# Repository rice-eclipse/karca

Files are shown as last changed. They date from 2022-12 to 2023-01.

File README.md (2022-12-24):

# kARCA: An engine controller PCB for Rice Eclipse

kARCA is Rice Eclipse's next generation of engine controller boards.
Its intended use is for data collection and valve actuation control on the Titan and Proxima rocket
motors.

It was designed in 2022 by Rice Eclipse.

## Usage

This board was designed in [KiCAD](https://www.kicad.org/).
Exports (such as gerber files) should be stored in the `target` directory (covered by gitignore).

It connects to a Raspberry Pi running our custom controller software,
[`slonk`](https://github.com/rice-eclipse/slonk), which in turn interfaces with the user dashboard
[`slonkboard`](https://github.com/rice-eclipse/slonkboard).

## Further documentation

A full overview of the design of kARCA is available in [docs/karca.md](docs/karca.md).

## License

This design is licensed under the Creative Commons Attribution-ShareAlike 4.0 International license
(CC BY-SA 4.0).

For more information, refer to [LICENSE.md](LICENSE.md).

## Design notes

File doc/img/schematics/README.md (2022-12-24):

# How to generate these files

In order to generate the SVG files in this directory, simply navigate to the top level of the
`kARCA` schematic and run `File -> Plot` with this directory as the target directory.

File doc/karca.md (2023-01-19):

# kARCA Design Outline

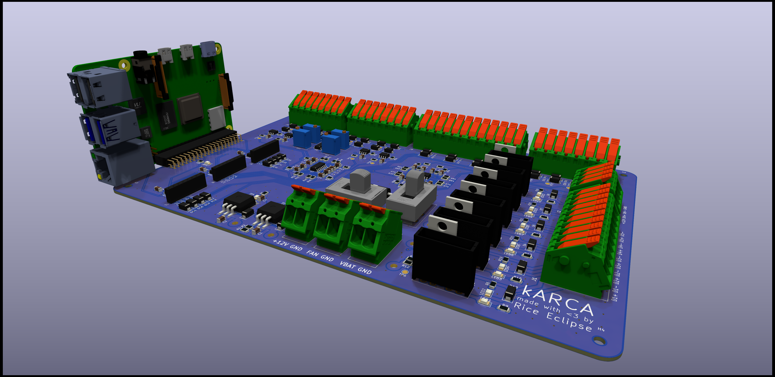
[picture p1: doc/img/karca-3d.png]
3D render of kARCA PCB.


This design outline is inteded as a reference for future Rice Eclipse members who either need to
edit the design of kARCA or better understand it.

It is also intended to be a comprehensive spec for working with the board.

## Project Motivation

Rice Eclipse is a student-run organization which designs, builds, and tests its own rocket motors.
To furnish this process, we build our own engine controller electronics systems from scratch.
`kARCA` is the latest revision of Eclipse's controller hardware: it communicates with a user-facing
dashboard to allow the user to control the engine in real time.

`kARCA` is part of a larger hardware and software stack which is essential to Eclipse's engine
testing system.
The user-facing dashboard, [`slonkboard`](https://github.com/rice-eclipse/slonkboard) is a
front-end application which allows mission control to easily use the controller.
Inside of the `kARCA` controller, a Raspberry Pi runs the controller software, `slonk`, which
receives messages from `slonkboard` and executes them, while also logging data and transmitting it
to `slonkboard`.

`kARCA` is intended as a replacement to an older control board, called the "Mk1.1 engine
controller."
The main reason for this replacement is because it's showing its age: the Mk1.1 controller was
designed for smaller valves and with fewer capabilities than its replacement.
In addition, a fire caused irreparable damage to one of the pressure transducer amplifiers on the
controller hardware.

## Requirements

kARCA has a few client needs that it must support for Rice Eclipse's Titan and Proxima rocket
motors.
It must:

1. Collect data from 4 load cells.
1. Collect data from 4 pressure transducers.
1. Collect data from 4 thermocouples.
1. Control the ignition system, driving up to 50 amps at 12 volts to the igniters.
1. Control 5 valves, each consuming up to 1 amp at 12 volts, by user command.
1. Transmit real-time data on load cells, pressure transducers, thermocouples, and valve actuation
   states to the user.

## Design

### Power regulation

Linear dropout regulators.

Power management consists of 3 separate voltage levels: 12 volts, 10 volts, and 5 volts.

The 12 volt lines are used for powering the solenoid driver circuits, the router, and the fan.
The 10 volt line is used for powering the analog amplification hardware (with the exception of the
load cell instrumentation amplifiers) and the pressure transducers.
The 5 volt line is used for powering the Raspberry Pi, the ADCs, the instrumentation amplifiers,
the thermocouple breakout boards, and the load cell.

The 5 volt and 10 volt lines are both supplied by linear dropout (LDO) regulators.
These regulators have the benefit of being stupid-simple at the cost of poor efficiency.
We've included flyback Schottky diodes on each regulator to hopefully reduce the risk of
reverse-biasing damanging the regulators.

_Note for future designs: it is possible to remove the 10V line from the design and substitute the
12V line.
The 10V line was only kept for backward compatibility, not for any material value._

The status light LED13 is lit when power is supplied to the 12V battery line.
LED14 and LED15 are lit when the LDO regulators for 10V and 5V respectively are working.

### Data collection

#### Load cells

Load cell amplification and filtering.

A load cell is a linear device used to measure force.
Power is supplied to the load cell through a positive and negative terminal, and then the load cell
returns a differential output.
The differential voltage $V_{\mathit{dm}}$ grows linearly with the force on the load cell.
If the voltage given to the load cell is $V_{\mathit{DD}}$, the output voltage $V_{\mathit{dm}}$ is
linearly proportional to the input voltage and the load $F$ via the constants $r$ and $FS$.

$$
V_{\mathit{dm}} = \frac{r}{\mathit{FS}} V_{\mathit{DD}} F
$$

$\mathit{FS}$ is the full-scale force of the load cell, and $r$ is the mV/V rating of the load cell.
Typically, $r$ is very small, so a high amount of amplification is needed to get an ADC-readable
signal.
Additionally, since $V_{\mathit{dm}}$ is a differential-mode signal, we must use an instrumentation
amplifier to convert the differential voltage to an absolute voltage.

On `kARCA`, there are two amplification stages for each load cell channel.
The first stage is an instrumentation amplifier, which amplifies the voltage measured and also
shifts the signal to a differential-mode value.
The second stage is an anti-aliasing filter, which low-passes the analog signal from the
instrumentation amplifier and also amplifies it further.

The total gain in the load cell amplifier is the product of the gains of the two stages.
The instrumentation amplifier has a gain of
$1 + \frac{20 \text{k} \Omega}{200 \Omega} = 101$, while the anti-aliasing filter has a
gain of $1 + \frac{15 \text{k} \Omega}{10 \text{k} \Omega} = 2.5$, yielding a final gain of 252.5.

The
[load cell for the Titan rocket motor](https://prod-edam.honeywell.com/content/dam/honeywell-edam/sps/siot/en-us/products/test-and-measurement-products/load-cells/low-profile/model-41-series/documents/sps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)
has a scale of 3mV/V and a full-scale force of 3000, yielding an output voltage equal to the load
$F$ times $1.2625 \frac{\text{mV}}{\text{lb f}}$.
This corresponds to a full-scale range of 3960 lb f.

At extremely high loads, the load cell amplifier could ouput voltages greater than 5 V to the ADC.
This would likely damage the ADC, so we included Schottky diodes to clamp the voltage below 5.5 V.

#### Pressure transducers

Pressure transducer anti-aliasing and amplifier.

Our pressure transducers are 4-20 mA devices.
This means that when supplied with a voltage greater than 8 V, the pressure transducers will pull
a current as an affine transform of the pressure (4 mA for 0 psi g, and 20 mA for 1000 psi g).

To convert the current to a voltage, we place the pressure transducer in series with a 22 $\Omega$
resistor, yielding an input voltage between 0.088 and 0.44 V.
Since the supply voltage is 10 V, the voltage given to the pressure transducer will never be below
9.66 V, which leaves plenty of headroom past the minimum 8 V requirement.

We then amplify the input voltage by a gain of 10.22, yielding a minimum output voltage of 0.898 V
and a maximum of 4.5 V.
Although we aren't using the full scale, it's "good enough" for our needs, giving us a resolution of
0.34 psi.
The gain of the amplifier is determined by the ratio of the feeback and gain resistors on the output
of the amplifier.
The gain for each channel is the same, so we only provide a sample formula for PT1's gain below.

$$
G = 1 + \frac{R_{73}}{R_{75}}
$$

Additionally, we anti-alias the pressure transducer signal with a two-pole Sallen-Key low-pass
filter.
The cutoff frequency is identical across all four PT channels, and is determined by the values of the input resistors and capacitors in the amplifier.
We provide a sample formula for PT1's gain below.

$$
f_c = \frac{1}{2 \pi \sqrt{R_{68} R_{69} C_{28} C_{26}}}
$$

Since the pressure transducer anti-aliasing amplifier is supplied by 10 V, we also include a set of
Schottky diodes to prevent the amplifier from sending too high of a voltage to the ADC.

#### Thermocouples

Thermocouple schematics.

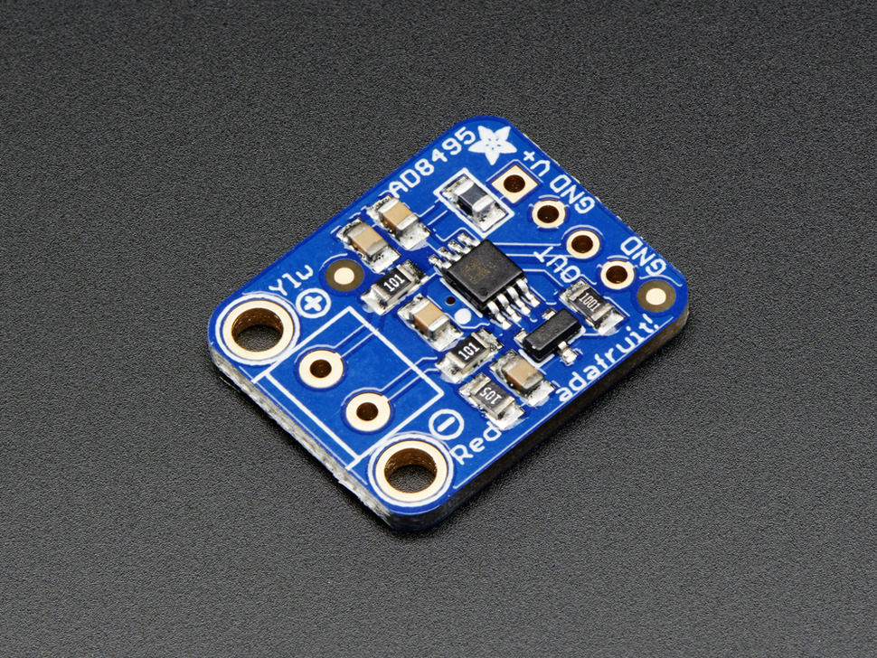
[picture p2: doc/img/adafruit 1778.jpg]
Adafruit AD8495 amplifier.


We use an [Adafruit AD8495](https://www.adafruit.com/product/1778) (part number 1778) amplifier
breakout board, which gives a voltage between 0 and 5V as an affine function of the measured
thermocouple temperature.
As a result, no amplification is needed and we can simply run the result directly to the ADC.
This makes the thermocouple data acquisition the easiest part of the design.
On the board end, only 3 connections are needed: positive voltage source, ground, and an analog
input.

However, the breakout board used only supports K-type thermocouples.
If, in the future, we decide to use other thermocouples, we may need to consider other avenues of
approach.

### Valve actuation

Valve drivers and ignition driver.

### Ignition system

As far as the `kARCA` PCB is concerned, the ignition system is just another valve.
Externally, though, the ignition system is a two-step sequence of relays.

## Pinouts

This is intended as a reference for programmers working on `slonk`,

### Raspberry Pi

| Number | Raspberry Pi function | GPIO ID | Board function |
| -----: | --- | ---: | --- |
| 1 | +3.3V | - | - |
| 2 | +5V | - | +5V |
| 3 | GPIO | 2 | - |
| 4 | +5V | - | +5V |
| 5 | GPIO | 3 | - |
| 6 | GND | - | GND |
| 7 | GPIO | 4 | - |
| 8 | UART0 TX | 14 | - |
| 9 | GND | - | GND |
| 10 | UART0 RX | 15 | - |
| 11 | GPIO | 17 | Driver 6 control |
| 12 | GPIO | 18 | - |
| 13 | GPIO | 27 | Driver 5 control |
| 14 | GND | - | GND |
| 15 | GPIO | 23 | Driver 4 control |
| 16 | GPIO | 23 | - |
| 17 | +3.3V | - | - |
| 18 | GPIO | 24 | - |
| 19 | SPI0 MOSI | 10 | SPI MOSI |
| 20 | GND | - | GND |
| 21 | SPI0 MISO | 9 | SPI MISO |
| 22 | GPIO | 25 | ADC1 CS |
| 23 | SPI0 SCLK | 11 | SPI CLK |
| 24 | SPI0 CS0 | 8 | ADC2 CS |
| 25 | GND | - | GND |
| 26 | SPI0 CS1 | 7 | ADC3 CS |
| 27 | I2C EEPROM data | - | - |
| 28 | I2D EEPROM clock | - | - |
| 29 | GPIO | 5 | Heartbeat |
| 30 | GND | - | GND |
| 31 | GPIO | 6 | Driver 3 control |
| 32 | GPIO | 12 | - |
| 33 | GPIO | 13 | Driver 2 control |
| 34 | GND | - | GND |
| 35 | GPIO | 19 | Driver 1 control |
| 36 | GPIO | 16 | - |
| 37 | GPIO | 26 | - |
| 38 | GPIO | 20 | - |
| 39 | GND | - | GND |
| 40 | GPIO | 21 | - |

### ADC1 - Load cells

| Channel | Use |
| --- | --- |
| 0 | LC1 |
| 1 | LC2 |
| 2 | LC3 |
| 3 | LC4 |
| 4 | unused |
| 5 | unused |
| 6 | unused |
| 7 | unused |

### ADC2 - Pressure transducers

| Channel | Use |
| --- | --- |
| 0 | PT1 |
| 1 | PT2 |
| 2 | PT3 |
| 3 | PT4 |
| 4 | unused |
| 5 | unused |
| 6 | unused |
| 7 | unused |

### ADC3 - Thermocouples

| Channel | Use |
| --- | --- |
| 0 | TC1 |
| 1 | TC2 |
| 2 | TC3 |
| 3 | TC4 |
| 4 | unused |
| 5 | unused |
| 6 | unused |
| 7 | unused |

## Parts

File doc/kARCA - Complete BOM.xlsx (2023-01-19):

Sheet: Totals
GRAND TOTAL: | $447.39

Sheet: Box
Ordered | Vendor | Manufacturer | Part Number | Description | Price | Quantity/package | Quantity/Assembly | Quantity to Purchase | Total price | Comments | Link
x | Amazon | GDQLCNXB |  | 5-pin XLR female connector | $12.99 | 5 | 4 | 1 | $12.99 |  | https://www.amazon.com/GDQLCNXB-Speaker-Microphone-Connector-Housing/dp/B0B1X4JXYX
x | Amazon | CNLINKO |  | 2-pin LP20 connector set | $15.99 | 1 | 3 | 4 | $63.96 |  | https://www.amazon.com/CNLINKO-waterproof-connector-locking-connect/dp/B07WJRWCJ2
x | Amazon | Zulkit | NBF-32422 | Plastic Electrical Box | $115.99 | 1 | 1 | 1 | $115.99 | consider alternatives if it goes out of stock | https://www.amazon.com/dp/B09YTYJP1N/ref=twister_B07RPNWC8V?_encoding=UTF8&th=1
x | Amazon | Gebildet |  | JD1912 Car Relay Harness 12V 40A | $8.49 | 2 | 1 | 1 | $8.49 |  | https://www.amazon.com/ARTGEAR-Harness-Color-Labeled-Automotive-Motorcycle/dp/B078T8CMF6?th=1
 | Amazon | Ximoon |  | 12V Power Trim Solenoid Switch | $13.99 | 1 | 1 | 1 | $13.99 |  | https://www.amazon.com/Ximoon-Solenoid-Outboard-89-96158T-89-846070/dp/B07JRC7WJ2
 | Amazon | Piezo |  | Piezo Buzzer 12V 100dB | $9.99 | 2 | 1 | 1 | $9.99 |  | https://www.amazon.com/Icstation-85dB-Active-Piezo-Electronic/dp/B01LAYWUDO
 | Amazon | DaierTek |  | 12 Volt Toggle Switch Safety Cover Guard | $7.99 | 1 | 1 | 1 | $7.99 |  | https://www.amazon.com/DaierTek-125VAC-Waterproof-Automotive-Aircraft/dp/B07T6YNRZS
 | Amazon | Monoprice |  | flat cat5 cable 3ft | $4.31 | 1 | 1 | 1 | $4.31 |  | https://www.amazon.com/Monoprice-Cat5e-Ethernet-Patch-Cable/dp/B00ACR5SD0
 | Amazon |  |  | Anderson connector kit | $15.98 |  |  |  | $15.98 |  | https://www.amazon.com/Powerpole-Connectors-Assortment-Disconnect-Unassembled/dp/B07CB121LL
 | McMaster-Carr |  | 90975A002 | Tee Nut, #4-40 | $14.46 | 100 | 4 | 1 | $14.46 |  | https://www.mcmaster.com/90975A002/
 | McMaster-Carr |  | 96068A105 | Thread Forming Screw for Plastic, No.4 x 0.5" Long | $6.18 | 100 | 36 | 1 | $6.18 | Mounting screws for XLR connectors | https://www.mcmaster.com/90434A115/
 | McMaster-Carr |  | 9697T3 | 14AWG Paired Red/Black Wire - 25 Feet | $18.75 | 1 | 1 | 1 | $18.75 |  | https://www.mcmaster.com/9697T3/
 | McMaster-Carr |  | 8054T13 | 22AWG Red Wire - 25 Feet | $3.58 | 1 | 1 | 1 | $3.58 |  | https://www.mcmaster.com/8054T13
 | McMaster-Carr |  | 8054T13 | 22AWG Black Wire - 25 Feet | $3.58 | 1 | 1 | 1 | $3.58 |  | https://www.mcmaster.com/8054T13
 | McMaster-Carr |  | 8054T13 | 22AWG Blue Wire - 25 Feet | $3.58 | 1 | 1 | 1 | $3.58 |  | https://www.mcmaster.com/8054T13
 | McMaster-Carr |  | 8054T13 | 22AWG White Wire - 25 Feet | $3.58 | 1 | 1 | 1 | $3.58 |  | https://www.mcmaster.com/8054T13
 | McMaster-Carr |  | 8054T13 | 22AWG Green Wire - 25 Feet | $3.58 | 1 | 1 | 1 | $3.58 |  | https://www.mcmaster.com/8054T13
 | Mouser | Amphenol | 523-AC3FAV-AU-PRE | 3-pin XLR female connector | $0.81 | 1 | 13 | 15 | $12.18 |  | https://www.mouser.com/ProductDetail/Amphenol-Audio/AC3FAV1-AU-PRE?qs=4QugYJNEYLfIiuxU%2Fbda%252Bw%3D%3D
 | OEDK |  |  | 1/4" thick plywood bottom board for box | $5.00 | 1 | 1 | 1 | $5.00
 | Wire | Wire
 |  |  |  |  |  |  |  | TOTAL: | $328.16

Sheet: Sensors and External Components
Vendor | Manufacturer | Part Number | Description | Price | Quantity/package | Quantity/Assembly | Quantity to Purchase | Total price | Comments | Link
 | Honeywell | 41-DN | 3000lb Pancake Load Cell; 3mV/V |  | 1 | 1 | 0 |  | Titan II load cell | https://prod-edam.honeywell.com/content/dam/honeywell-edam/sps/siot/en-us/products/test-and-measurement-products/load-cells/low-profile/model-41-series/docume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
 | Phidgets | CZL301C | 100kg (220lb) S-Type Load Cell | $45.00 | 1 | 1 | 0 |  | Luna/Proxima load cell | https://www.phidgets.com/?tier=3&catid=9&pcid=7&prodid=229
 | Omega | PX119-1KGI | Pressure Transducer, 4-20mA, 0-1000psig |  | 1 | 4 | 0 |  | Pressure transducer | https://assets.omega.com/pdf/test-and-measurement-equipment/pressure/pressure-transducers/PX119.pdf
 | Adafruit | 270 | Thermocouple, Type-K, 900C | $9.95 | 1 | 3 | 0 |  | Non-oxidizer thermocouples | https://www.adafruit.com/product/270
 | Adafruit | 1778 | Analog Output K-Type Thermocouple Amplifier - AD8495 Breakout | $11.95 | 1 | 4 | 0 |  |  | https://www.adafruit.com/product/1778

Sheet: PCB (assembled by Eclipse)
Vendor | Vendor Number | Manufacturer | Description | Price | Quantity/package | Quantity/Assembly | Quantity to Purchase | Total price | Comments | Link
JLC |  |  | ARCA PCB |  |  | 1 | 5 |  | JLC requires minimum purchase of 5 PCBs, of which 2 is the minimum amount to buy assembled. Price should include all parts assembled by JLC as well.
Connectors
Mouser | 200-SSQ12002GDRA | Samtec | 2x20 90 degree female header connector | $10.72 | 1 | 1 | 1 | $10.72 | Raspberry Pi connector. Consider buying cheaper from Adafruit? | https://www.mouser.com/ProductDetail/Samtec/SSQ-120-02-G-D-RA?qs=rU5fayqh%252BE1h5x2E2Y6bfA%3D%3D
Mouser | 571-215297-8 | TE Connectivity | 1x8 Header Pin Female | $1.61 | 1 | 3 | 3 | $4.83
Mouser | 651-1190370 | Phoenix Contact | LPTA 8 Position Connector | $5.78 | 1 | 3 | 3 | $17.34
Mouser | 651-1190363 | Phoenix Contact | LPTA 2 Position Connector | $1.44 | 1 | 3 | 3 | $4.32
Mouser | 651-1190365 | Phoenix Contact | LPTA 4 Position Connector | $2.84 | 1 | 1 | 1 | $2.84
Mouser | 651-1190372 | Phoenix Contact | LPTA 10 Position Connector | $7.20 | 1 | 1 | 1 | $7.20
Mouser | 651-1190374 | Phoenix Contact | LPTA 12 Position Connector | $8.65 | 1 | 1 | 1 | $8.65
Passive (We mount)
Mouser | 863-1N5822RLG | ON Semiconductor | DO201 Schottky Rectifying Diode | $0.59 | 1 | 1 | 1 | $0.59 |  | https://www.mouser.com/ProductDetail/onsemi/1N5822RLG?qs=y2kkmE52mdOHZAAYnNZhxg%3D%3D
Mouser | 652-3296W-1-303LF | Bourns | 30k Trimming Potentiometer | $2.35 | 1 | 4 | 4 | $9.40
ICs
Mouser | 579-MCP6N11-100E/SN | Microchip Technology | 500 kHz Instrumentation Amplifier | $1.77 | 1 | 4 | 4 | $7.08
Mouser | 512-FQP30N06L | ON Semiconductor | NMOS transistor | $1.97 | 1 | 6 | 6 | $11.82
Other |  |  |  |  |  |  |  | $0.00
Mouser | 576-178.6165.0001 | Littelfuse | FLR Fuse Holder | $4.31 | 1 | 6 | 6 | $25.86
Mouser | 576-0287005.PXCN | Littelfuse | 5A ATO Fuse | $0.32 | 1 | 6 | 6 | $1.92
Mouser | 611-S101031MS02Q | C&K | Slide Switch 6A | $3.33 | 1 | 2 | 2 | $6.66
 |  |  |  |  |  |  |  | $0.00
 |  |  |  |  |  |  | TOTAL: | $119.23

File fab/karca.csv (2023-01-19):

Comment | Designator | Footprint | LCSC
MCP3208-CI/SL | ADC1,ADC2,ADC3 | Package_SO:SOIC-16_3.9x9.9mm_P1.27mm | C16939
10u | C1,C2,C3,C4 | Capacitor_SMD:C_1206_3216Metric | C92797
100n | C13,C18,C19,C20,C21,C33 | Capacitor_SMD:C_1206_3216Metric | C377067
1u | C5,C6,C7,C10 | Capacitor_SMD:C_1206_3216Metric | C85867
1n | C8,C9,C11,C12,C14,C15,C16,C17,C25,C26,C27,C28,C29,C30,C31,C32 | Capacitor_SMD:C_1206_3216Metric | C1845
Screw_Terminal_01x02 | CON_BAT1,CON_FAN1,CON_ROUTER1 | 1190363:1190363
1N5822RLG | D1 | Diode_THT:D_DO-201AD_P15.24mm_Horizontal
CDBA340-HF | D2,D3,D4,D5,D6,D7,D8,D9,D10,D11,D12,D13,D14,D15,D16,D17,D18,D19,D20,D21,D22,D23,D24,D25,D26,D27,D28,D29,D30,D31,D32,D33,D34,D35,D36,D37,D38,D39,D40,D41,D42,D43,D44,D45,D46,D47,D48,D49 | Diode_SMD:D_SMA | C14996
178.6165 | F1,F2,F3,F4,F5,F6 | 178.6165:17861650002
MountingHole | H1,H2,H3,H4 | MountingHole:MountingHole_3.2mm_M3
Screw_Terminal_01x10 | J1 | 1190372:1190372
Screw_Terminal_01x04 | J2 | 1190365:1190365
Screw_Terminal_01x08 | J3,J4,J6 | 1190370:1190370
2540-5 | J33 | Connector_PinSocket_2.54mm:PinSocket_2x20_P2.54mm_Horizontal
Conn_01x08_Female | J5,J7,J8 | Connector_PinSocket_2.54mm:PinSocket_1x08_P2.54mm_Vertical
Screw_Terminal_01x12 | J9 | 1190374:1190374
GRN | LED1,HBT1,LED3,LED5,LED7,LED9,LED11 | LED_SMD:LED_1206_3216Metric | C499462
RED | LED13,LED14,LED15 | LED_SMD:LED_1206_3216Metric | C84270
YLW | LED2,LED4,LED6,LED8,LED10,LED12 | LED_SMD:LED_1206_3216Metric | C434441
FQP30N06 | Q1,Q2,Q3,Q4,Q5,Q6 | Package_TO_SOT_THT:TO-220-3_Vertical
1k | R1 | Resistor_SMD:R_1206_3216Metric | C294117
68k | R2,R37,R38,R40,R41,R42,R43,R44,R45,R66,R67,R68,R69,R76,R77,R78,R79 | Resistor_SMD:R_1206_3216Metric | C102381
820 | R3 | Resistor_SMD:R_1206_3216Metric | C229812
20K | R30,R31,R32,R36 | Resistor_SMD:R_1206_3216Metric | C114940
200 | R33,R34,R35,R39 | Resistor_SMD:R_1206_3216Metric | C114939
10k | R4,R8,R11,R14,R15,R23,R25,R47,R49,R51,R53 | Resistor_SMD:R_1206_3216Metric | C132649
15k | R46,R48,R50,R52 | Resistor_SMD:R_1206_3216Metric | C1493
300 | R5 | Resistor_SMD:R_1206_3216Metric | C17887
910 | R6,R9,R16,R17,R18,R19,R20,R21,R26,R27,R28,R29 | Resistor_SMD:R_1206_3216Metric | C429066
DNP | R7,R10,R12,R13,R22,R24 | Resistor_SMD:R_1206_3216Metric
22 | R70,R72,R80,R82 | Resistor_SMD:R_1206_3216Metric | C17958
47k | R71,R73,R81,R83 | Resistor_SMD:R_1206_3216Metric | C168584
5.1k | R74,R75,R84,R85 | Resistor_SMD:R_1206_3216Metric | C26033
150 | R89 | Resistor_SMD:R_1206_3216Metric | C17917
30k | RV1,RV2,RV3,RV4 | Potentiometer_THT:Potentiometer_Bourns_3296W_Vertical
S101031MS02Q | SW1,SW2 | S101031MS02Q:S101031MS02Q
TestPoint | TP1,TP2,TP3,TP4,TP5,TP6,TP7,TP8,TP9,TP10,TP11,TP12,TP13,TP14,TP15,TP16,TP17,TP18,TP19,TP20,TP21,TP22,TP23,TP24,TP25,TP26,TP27 | TestPoint:TestPoint_Pad_D2.0mm
LM1084-ADJ | U1 | Package_TO_SOT_SMD:TO-263-3_TabPin2 | C259971
LM1084-5.0 | U2 | Package_TO_SOT_SMD:TO-263-3_TabPin2 | C259973
MCP6N11 | U3,U4,U5,U6 | Package_SO:SOIC-8_3.9x4.9mm_P1.27mm
LM324 | U7,U8,U11 | Package_SO:SOIC-14_3.9x8.7mm_P1.27mm | C71035

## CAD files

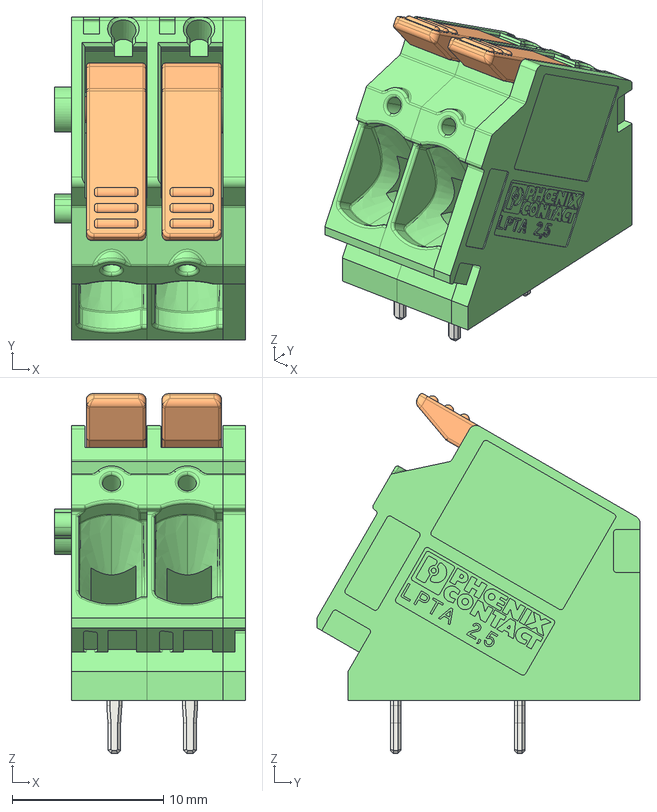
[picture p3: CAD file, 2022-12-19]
1190363/pxc_1190363_02_LPTA-2-5-2-5-0_3D.stp
12.6 x 21.4 x 23.8 mm
LP_LPT_2_5_3_50.2 x 4
AC_LPT_2_5_LEVER x 2
PK_LPTA_2_5_5_00.2 x 2
DK_LPTA_2_5_5_00

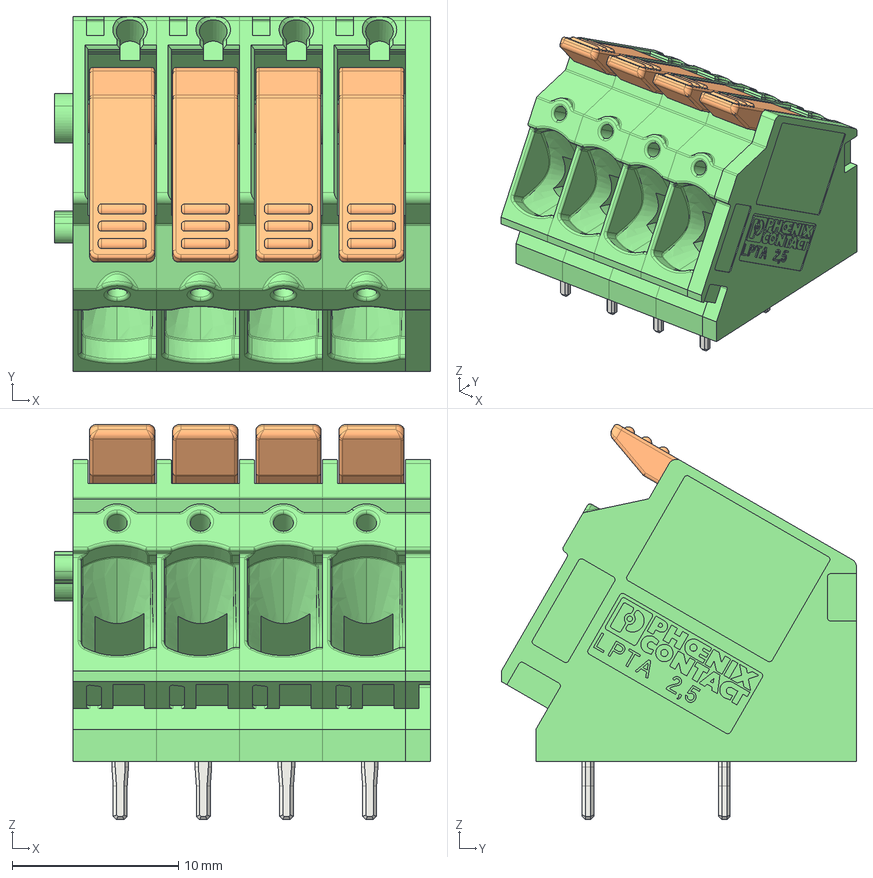
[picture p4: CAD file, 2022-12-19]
1190365/pxc_1190365_02_LPTA-2-5-4-5-0_3D.stp
22.6 x 21.4 x 23.8 mm
LP_LPT_2_5_3_50.2 x 8
AC_LPT_2_5_LEVER.2 x 4
PK_LPTA_2_5_5_00.2 x 4
DK_LPTA_2_5_5_00

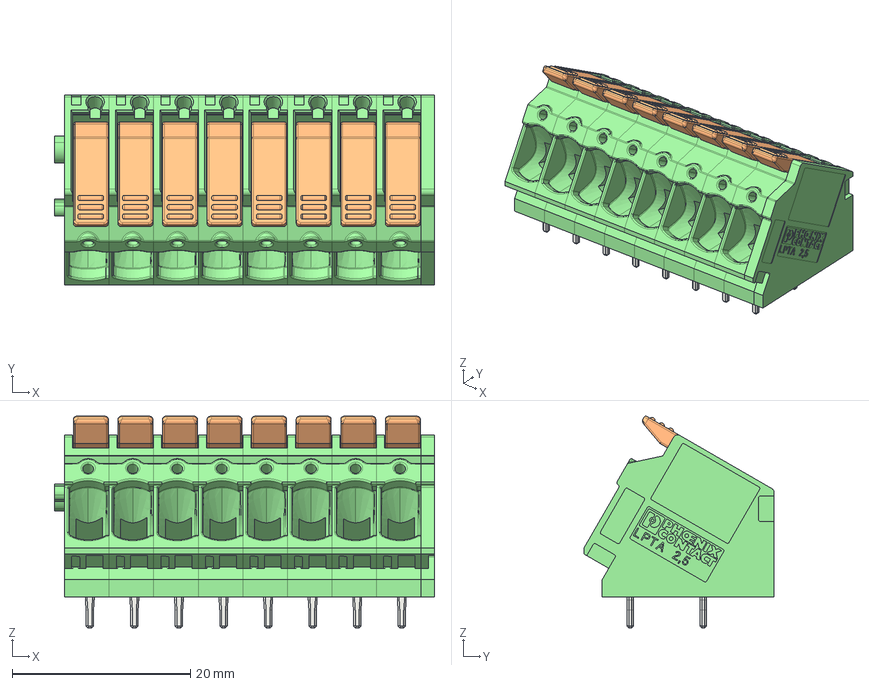
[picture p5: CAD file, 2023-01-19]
1190370/pxc_1190370_02_LPTA-2-5-8-5-0_3D.stp
42.6 x 21.4 x 23.8 mm
LP_LPT_2_5_3_50.2.5 x 16
AC_LPT_2_5_LEVER.2 x 8
PK_LPTA_2_5_5_00.7 x 8
DK_LPTA_2_5_5_00

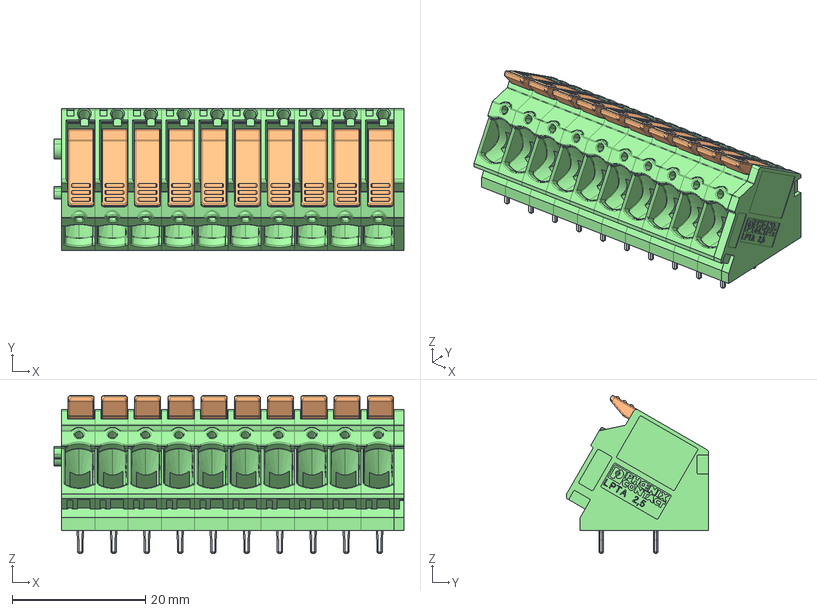
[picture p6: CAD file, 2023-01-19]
1190372/pxc_1190372_02_LPTA-2-5-10-5-0_3D.stp
52.6 x 21.4 x 23.8 mm
AC_LPT_2_5_LEVER.10 x 10
LP_LPT_2_5_3_50.2.7 x 20
PK_LPTA_2_5_5_00.7 x 10
DK_LPTA_2_5_5_00

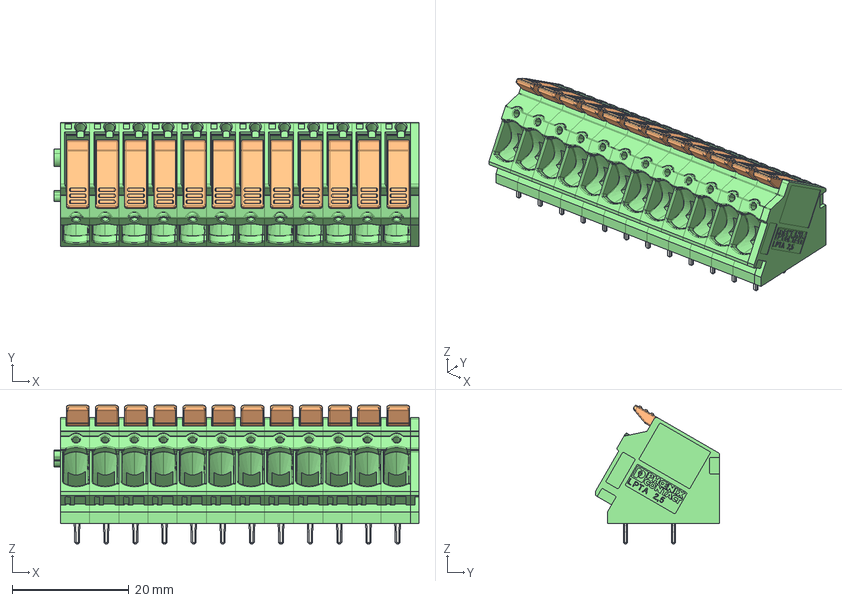
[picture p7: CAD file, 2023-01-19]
1190374/pxc_1190374_02_LPTA-2-5-12-5-0_3D.stp
62.6 x 21.4 x 23.8 mm
AC_LPT_2_5_LEVER.4 x 12
LP_LPT_2_5_3_50.5 x 24
PK_LPTA_2_5_5_00.7 x 12
DK_LPTA_2_5_5_00

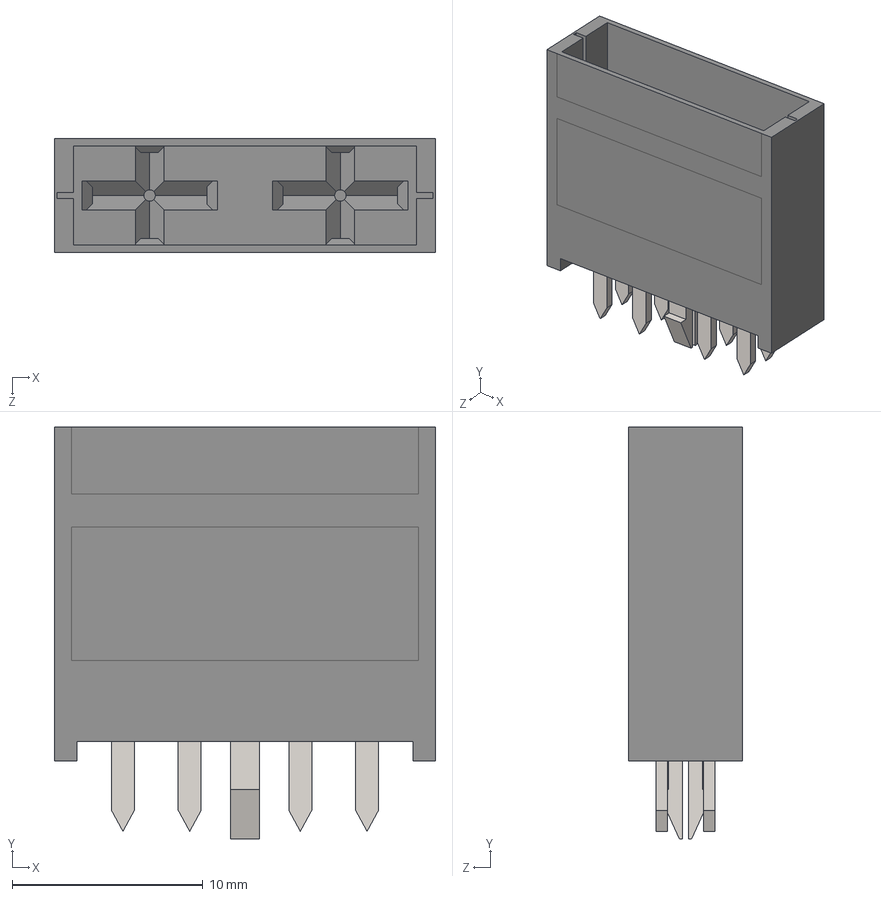
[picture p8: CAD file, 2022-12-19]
178.6165.0002/178.6165.0002.stp
20.0 x 21.6 x 6.00 mm

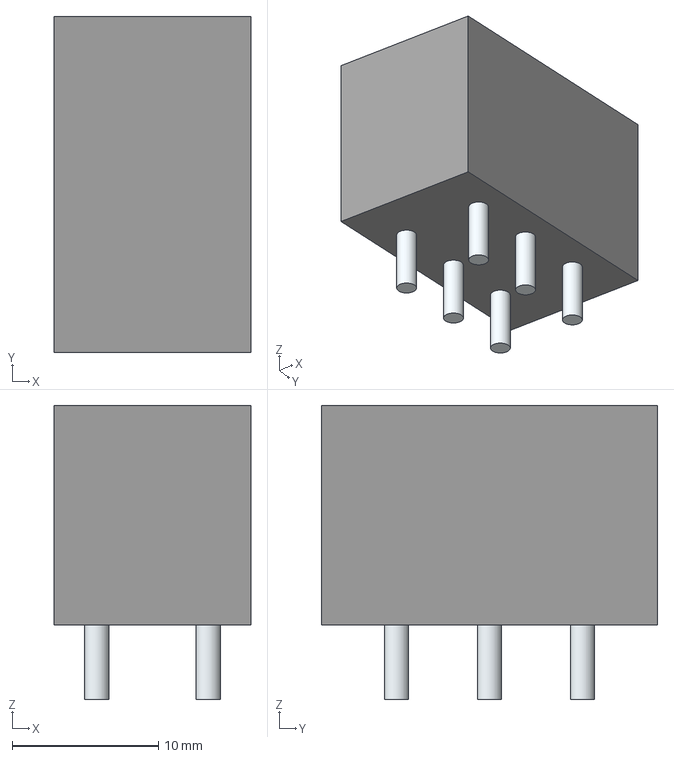
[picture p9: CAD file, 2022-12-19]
S101031MS02Q/S101031MS02Q.stp
13.5 x 23.0 x 20.1 mm
Leads x 6

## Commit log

2022-09-14 Half complete regulator schematic to start working off of
    [karca_v1_0.kicad_pcb, karca_v1_0.kicad_sch]
2022-09-14 unfuck git setup
    [karca.kicad_pcb, karca.kicad_sch]
2022-09-14 i am very smart. no person can match my intellectual prowess. chinese pcb manufacturers tremble before me
    [karca.kicad_pcb, karca.kicad_sch]
2022-09-18 secret arca meetings
    [drivers.kicad_sch, karca.kicad_sch, lc_anti_alias.kicad_sch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]
2022-09-18 Added pages
    [adc.kicad_sch, karca.kicad_sch, pi.kicad_sch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]
2022-09-25 first revision of full schematic copied over
    [adc.kicad_sch, drivers.kicad_sch, karca.kicad_sch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]
2022-09-25 added schematic pdf for review
    [adc.kicad_sch, drivers.kicad_sch, karca.kicad_sch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]
2022-10-17 added footprints and started schematic review revisions
    [adc.kicad_sch, drivers.kicad_sch, karca.kicad_sch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]
2022-10-20 schematic editing + creating some footprints
    [adc.kicad_sch, drivers.kicad_sch, karca.kicad_pcb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]
2022-10-23 updated all footprints, resolved most ERC & setup layout
    [1101M2S3CQE2.step, 3296W-1-303LF.step, adc.kicad_sch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]
2022-10-27 grouped components on PCB
    [adc.kicad_sch, drivers.kicad_sch, karca.kicad_pcb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]
2022-11-07 preliminary layout and started pwr plane config
    [1190363.PcbLib, 1190363.SchLib, 1190363.psm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]
2022-11-17 fixed pwr planes
    [karca.kicad_pcb]
2022-12-17 some minor schematic cleanup
    [adc.kicad_sch, drivers.kicad_sch, karca.kicad_pcb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]
2022-12-17 shuffle around some parts
    [1190363.PcbLib, 1190363.SchLib, 1190363.psm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]
2022-12-17 add overvoltage diodes
    [karca.kicad_pcb, karca.kicad_sch, lc_anti_alias.kicad_sch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]
2022-12-17 positioning for LC connectors
    [karca.kicad_pcb, karca.kicad_sch, lc_inamps.kicad_sch]
2022-12-17 complete arrangement for load cells
    [karca.kicad_pcb, karca.kicad_sch, lc_inamps.kicad_sch]
2022-12-18 laid out ignition and PTs
    [drivers.kicad_sch, karca.kicad_pcb, karca.kicad_sch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]
2022-12-18 nearly done with part layout
    [karca.kicad_pcb, pi.kicad_sch]
2022-12-18 finish putting shit together
    [karca.kicad_pcb, karca.kicad_sch, lc_inamps.kicad_sch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]
2022-12-18 copper pours done
    [karca.kicad_pcb, karca.kicad_sch, lc_inamps.kicad_sch]
2022-12-18 starting on routing
    [karca.kicad_pcb, karca.kicad_sch, lc_inamps.kicad_sch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]
2022-12-19 mostly finished routing
    [1101M2S3CQE2.step, 1190363.stp, S101031MS02Q.stp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]
2022-12-19 cleaned up bad hole sizes but now there are interferences
2022-12-19 not sure if anything has changed but this is the last commit before moving to two LCs
    [karca.kicad_sch, lc_inamps.kicad_sch, pi.kicad_sch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]
2022-12-20 enshrinkening of the board
    [adc.kicad_sch, drivers.kicad_sch, karca.kicad_sch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]
2022-12-20 done routing on shrunk board
    [adc.kicad_sch, karca.kicad_sch, regulators.kicad_sch]
2022-12-23 remove sheet borders from schematic pictures
2022-12-27 done schematiccing after design review
    [adc.kicad_sch, drivers.kicad_sch, karca.kicad_sch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]
2022-12-27 cleaned up PT footprint
    [drivers.kicad_sch, karca.kicad_sch, lc_inamps.kicad_sch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]
2022-12-28 waiting on mouser for footprints
    [drivers.kicad_sch, karca.kicad_pcb, karca.kicad_sch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]
2022-12-28 ready for fab
    [drivers.kicad_sch, karca.kicad_sch, pxc_1190364_02_LPTA-2-5-3-5-0_3D.stp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]
2022-12-29 solid fill for current paths
2022-12-29 final rev for jlc
    [drivers.kicad_sch, karca.kicad_sch, pi.kicad_sch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]
2022-12-29 possible fix for output impedance on load cell reference voltage; not yet in PCB
    [karca.kicad_sch, lc_inamps.kicad_sch]
2023-01-03 started on opamp arrangement
    [lc_inamps.kicad_sch, regulators.kicad_sch]
2023-01-03 my body is a machine that takes in peanut m&ms and puts out rocket engine controllers
    [drivers.kicad_sch, karca.kicad_sch, lc_inamps.kicad_sch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]
2023-01-08 add incomplete bom
    [kARCA - Complete BOM.xlsx]
2023-01-10 create fab data for karca
    [kARCA - Complete BOM.xlsx]
2023-01-10 add csvs to fab outputs
    [karca.csv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]
2023-01-10 updated bom with box stuff
    [kARCA - Complete BOM.xlsx]
2023-01-10 added lp20 connectors to karca bom
    [kARCA - Complete BOM.xlsx]
2023-01-10 added jd1912 type relay for ignition to karca bom
    [kARCA - Complete BOM.xlsx]
2023-01-10 karca BOM done
    [kARCA - Complete BOM.xlsx]
2023-01-12 updated load cell count to 4
    [kARCA - Complete BOM.xlsx]
2023-01-19 make karca pcb blue
2023-01-19 clean up unused libraries
    [S101031MS02Q.stp]
